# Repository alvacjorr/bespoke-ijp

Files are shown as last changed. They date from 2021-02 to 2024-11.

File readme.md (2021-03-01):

# bespoke-ijp



This repository is used for documents / code / notes related to the controller and software of the IEB bespoke inkjet printing rig. 
## Folder Structure
| Folder |  Description  | 
| ---| ---|
| `/application` | Code for the application/GUI |
| `/embedded` | Code for the uSteppers |
| `/docs` | Documentation |

## Workflow - Basics 
#### How do I get a copy of this repo?
- Install **Git**: https://help.github.com/en/github/getting-started-with-github/set-up-git
- Open up a terminal / command prompt and clone this repository: `git clone https://github.com/thekeeno/bespoke-ijp` which will give you a local copy of the main branch in the repository

#### Do I have to use a terminal?
- You can also use Git GUIs, e.g. https://desktop.github.com/ or https://www.gitkraken.com/

#### How do I keep my local copy updated?
- If you are on the main branch you can type `git pull`

#### How can I add / submit my changes?
- **The main main branch is protected, so you will have to create a separate branch and open a pull request.**
- The `main` branch should always reflect the newest agreed on version of the repository
- Make sure you branch off the latest state of main, i.e. on main type `git pull` or use `git fetch`
- To create a new branch use: `git checkout -b [branchname]`, e.g. `git checkout -b mg/new_branch`
- Make changes to files / add new files
- Take a look at the summary of changed files: `git status` 
- Add the new files to be tracked: `git add .` (to add all new files) or `git add code.m` (to add specific file)
- Commit the new changes (this creates a snapshot of repository state): `git commit -m "Change parameter gamma to 0.5"`
- Copy your new local branch with the new commits to the Github repository: `git push -u origin mg/new_branch`

- **Before your changes can be merged:** Make sure that you integrate the changes on `main` that others might have added in the meantime. This can be achieved by pulling the `main` changes to yout machine and then *merging* or preferably *rebasing* your commits onto the latest `main` version. See [here](https://gist.github.com/blackfalcon/8428401#keeping-current-with-the-master-branch) for a more detailed explanation.
- On https://github.com/oxfordcontrol/OxVentControl/ click on `Pull requests` -> `New Pull Request`. 
- Select `base:main` and `compare:mg/new_branch`
- All the changes can then be discussed in that pull request before they are approved and added to the main branch.
#### Useful git commands:
- https://rogerdudler.github.io/git-guide/
- https://confluence.atlassian.com/bitbucketserver/basic-git-commands-776639767.html
- http://ohshitgit.com/

## Workflow - Making Git collaboration easier 
A few steps everyone should take to make collaboration with Git easier:

#### Commit early and often
One commit should reflect one meaningful change to the code. Especially if we work on lots of different things at the same time, it is helpful if we create one meaningful commit for each significant change to the code. Notice that you don't have to commit all current changes at the same time. If you changed something in `A.cpp` and something different in `B.cpp`, you can do:
```bash
git add A.cpp
git commit -m "Fixed printing in A."
git add B.cpp
git commit -m "Changed parameters in B."
```
#### Combine temporary commits / clean up your history
If your recent 4 commits look like this `Fixed ABC`, `Work in progress`, `Working version` `Ups small fix` and you want to open a pull request to add this to the code you should first combine these commits into one commit. This can be done with an interactive  `git rebase`. To select the last 4 commits to squash, type:
```bash
git rebase -i HEAD~4
```
This should open an editor and show something like this:
```bash
pick d94e78 Fixed ABC     --- older commit
pick 4e9baa Work in progress
pick afb581 Working version  
pick 643d0e Ups small fix --- newer commit
```
Pick the oldest commit and squash the other ones into it by editing the file and saving it like this:
```bash
pick d94e78 Fixed ABC     --- older commit
s 4e9baa Work in progress
s afb581 Working version  
s 643d0e Ups small fix --- newer commit
```
You can then write a commit message for this combined commit. Combining commits can be very powerful, **but keep in mind that this rewrites the git history. Therefore never use the rebase on a remote branch where you know that other people rely on your history.**

[More info](https://www.internalpointers.com/post/squash-commits-into-one-git)

#### Write meaningful commit messages


Commit messages should make it easy to understand what particular change the commit implements. For more complex cases it can be helpful to write more than one sentence. To do that use the commit command without the message flag:
```bash
git commit
```
your default editor will open and you can write a longer form commit message. If you don't like the default editor you can set another one with:
```bash
git config --global core.editor "vim"
```

Follow the 7 rules of a great Git commit message

1. Separate subject from body with a blank line
2. Limit the subject line to 50 characters
3. Capitalize the subject line
4. Do not end the subject line with a period
5. Use the imperative mood in the subject line
6. Wrap the body at 72 characters
7. Use the body to explain what and why vs. how

[from here](https://chris.beams.io/posts/git-commit/)

#### Visualise the git tree before you merge
In order to not cause chaos with merges, it is helpful to take a look at the git commit tree and see where you currently are with your branch and where the branch you want to merge into currently is. You can either use a software package like [Gitkraken](https://www.gitkraken.com/) or alternatively use the command-line with:
```bash
git log --graph --decorate --oneline
```
If this is too long to remember you can create a Git Alias. On Unix systems type:
```bash
vim ~/.gitconfig
```
and add the line
```
[alias]
  gr = git log --graph --decorate --oneline
```
to the file.
#### Integrate the latest changes before opening a PR
If you are on the branch `my_fix` and want to open a PR to merge into `target_branch`, double-check if in the meantime any other changes happened on `target_branch` that might cause problems. To integrate the latest changes checkout the target branch:
```bash
git checkout target_branch
git pull origin target_branch
git checkout my_fix
```
To integrate the changes you can either `rebase` or `merge`. Rebasing is the cleaner way of the two as it doesn't introduce new merge commits. It essentially replays all of your new commits in `my_fix` onto the latest commit of `target_branch`. In some cases this will not go smoothly and you'll have to fix the conflicts as the commits are applied. **Again note that the rebase will rewrite history, so only do that if you know nobody else relies on the commits that will be rewritten**.

[Merging vs. Rebasing](https://www.atlassian.com/git/tutorials/merging-vs-rebasing)

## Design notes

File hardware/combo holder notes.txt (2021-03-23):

nozzle dia 3.5
depth 12.7

minicut width 1
height 4.577

photofluor small dia 5
large dia 9
depth 20

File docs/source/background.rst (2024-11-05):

Background and Motivation
==========

This section explains the main motivations for the development of the bespoke-ijp system, as well as a description of some of the work that precedes it.
Much of this section is copied verbatim from Alva Orr's transfer report.

Inkjet Printing
***************

Inkjet printing is a digital, non-contact manufacturing method which, broadly speaking, consists of launching droplets of fluid from a nozzle onto a substrate.
Inkjet printing is a large market, with an estimated size of \$34 billion in 2019(Mordor Intelligence). 
The most familiar usage of inkjet printing is in reprographics, which makes up around 90\% of the market, and includes commodity devices like desktop inkjet printers.

In the case of this system, Drop-On-Demand (DOD) is used.

Predecessor System
********************

The predecessor to this system, which ran using smaller stepper motors on belts, over a LabVIEW controller, currently still lives in the Fluids Lab.
It is thoroughly documented in Ellis Parry's DPhil thesis, soon to be available on ORA.
However, it has some limitations, especially with proprietary driver compatibility and dependence on closed-source software.
The new bespoke-ijp system was therefore conceived to remedy these issues. The major improvements are set to include:

- Use of closed-loop position control for maximum repeatability
- Dedicated stepper driver chips
- All built on open-source platforms (Arduino, Python)
- Cross-platform compatability (Windows, Linux in the works)
- Optional closed-loop heating control
- Support for synchronised motion and piezo pulses
- Basic scripting language, built on GCode, to allow for printing of patterns and similar routines

Comparable Systems
******************

This system can be thought of as a low-cost, flexible DIY alternative to the MicroFab JetLab system installed in the Holder building.
Although the commercial JetLab system is very accurate and reliable, it is not capable of integrating complex observation systems such as multiple high-speed cameras.

Relevent Publications and Literature
************************************

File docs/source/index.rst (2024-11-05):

IEB Bespoke Inkjet Printing
=======================================

This manual is for the Bespoke IEB Inkjet Printing (IJP) rig, a collaborative project between the `Fluid Dynamics Lab <http://www2.eng.ox.ac.uk/fluidlab>`_ and `Soft Matter Photonics <http://www2.eng.ox.ac.uk/smp>`_ groups in the Oxford University Department of Engineering Science.
Currently the person responsible for building and maintaining this rig is Alva Orr.

This documentation is still a Work In Progress. If there's any glaring omissions, please contact alva.orr@queens.ox.ac.uk.

.. toctree::
   :caption: Contents
   :maxdepth: 4

   background
   userguide
   building
   programmer
   autodoc/modules
   funcgen
   issues

Indices and tables
==================

* :ref:`genindex`
* :ref:`modindex`
* :ref:`search`

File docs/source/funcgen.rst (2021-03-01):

Function Generator Setup
========================

Aim 
******

We want to generate 10kHz square waves, that ramp up and down to various amplitudes ~175V.
The ramp up should be configurable to either be linear at varying rates, or in steps.

How

****

Unfortunately, the Tektronics AFG-2021 has some weird behavior with arbitrary waveforms and AM.
So we use the AFG-2021 as the modulator, and have a different (GWINSTEK?) AFG generate the 10kHz carrier.

Configuration of the AFG-2021
*****************************

1-Shot mode. around 100mHz. Lower voltage 0V. Higher voltage 5V.

Equation comes from PC. 

Configuration of the other function Generator
**********************************************

Set up so that at 0V Mod, the waveform is 0V p-p, and at 5V Mod, the output is XV p-p.

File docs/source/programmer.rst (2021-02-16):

Programmer's Documentation
==========================

The code for this project is split into two parts - Python code for the GUI and C++ embedded code for the uSteppers.
When navigating this code, it is strongly recommended to use Visual Studio Code with the C++, Python, Git and Arduino extensions.

In addition, this documentation is assembled using sphinx and ReadTheDocs.com.

Embedded 
*********

The core of the embedded firmware is loosely based on a GCode parser included with the uStepper's examples, but extended and upgraded to include more commands.

GUI Code
********

The classes, modules and functions that make this software work are all documented in the Python Module Guide.
This section is intended instead as a loose overview of the way the GUI operates.

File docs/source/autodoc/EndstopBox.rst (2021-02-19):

EndstopBox module
=================

.. automodule:: EndstopBox
   :members:
   :undoc-members:
   :show-inheritance:

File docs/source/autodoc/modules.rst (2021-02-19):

src
===

.. toctree::
   :maxdepth: 4

   EndstopBox
   SequenceHandler
   XYSerialInterface
   XY_commander
   constants
   conversions
   embedding_in_qt_sgskip
   plotter_example
   port_finder
   psu_serial
   testpsu

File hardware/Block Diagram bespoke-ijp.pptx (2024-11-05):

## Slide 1

PC

Photofluor II Light Source

Polariser

RS232

JetDrive III

Nozzle Heatblock

GPD-43035
Power Supply

USB Camera

Γ

2

1

Polarised Optical Microscopy Path

Slide Holder

Shadowgraphy Path

H

T

LED

Γ

H

T

PhlatLight LED Driver

MAX31855

Analyzer + Camera

Γ

uStepper X

Motor X

Nozzle

DIGITAL OUT

Camera

LED

SPI

uStepper Y

Motor Y

Piezo Waveform

USB/Serial

TTL Trigger (5V)

Thermocouple Wire

Heater Cable (24V)

Heater Module

Thermocouple (K-Type)

Trigger Input

H

T

Γ

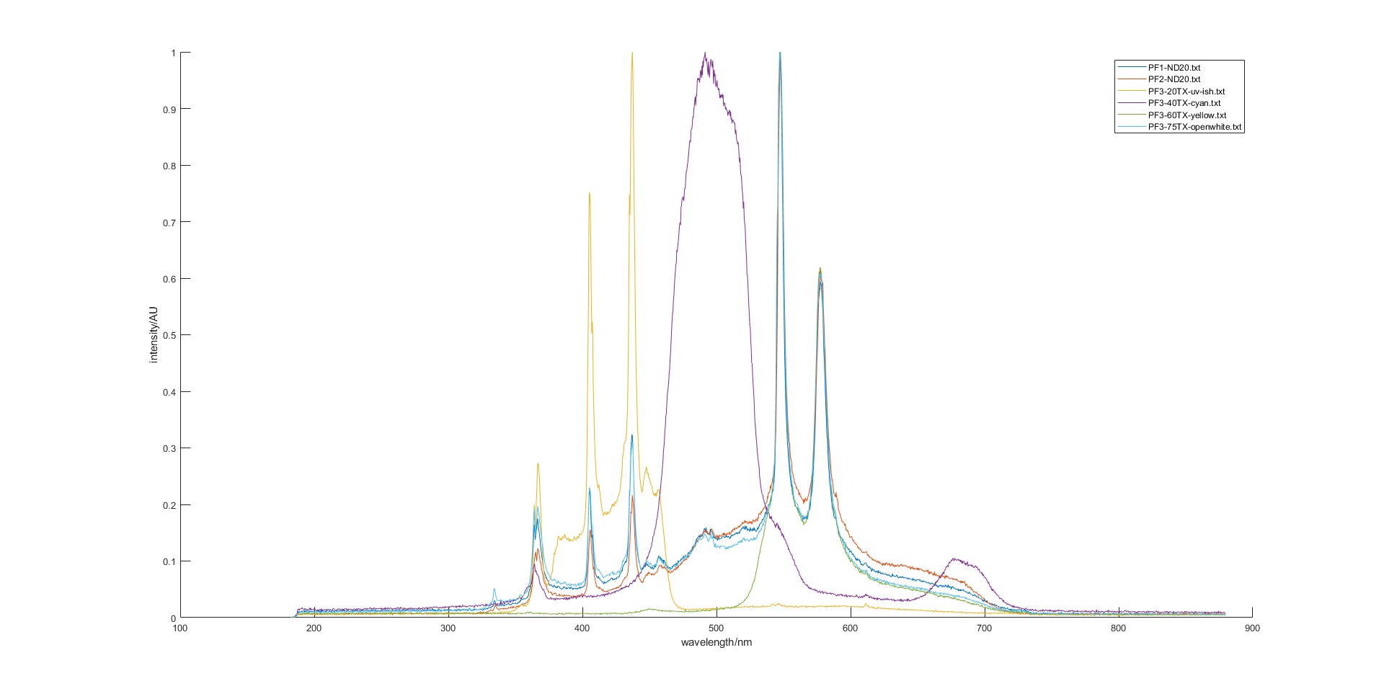
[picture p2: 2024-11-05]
photofluor_spectra/spectra.jpg

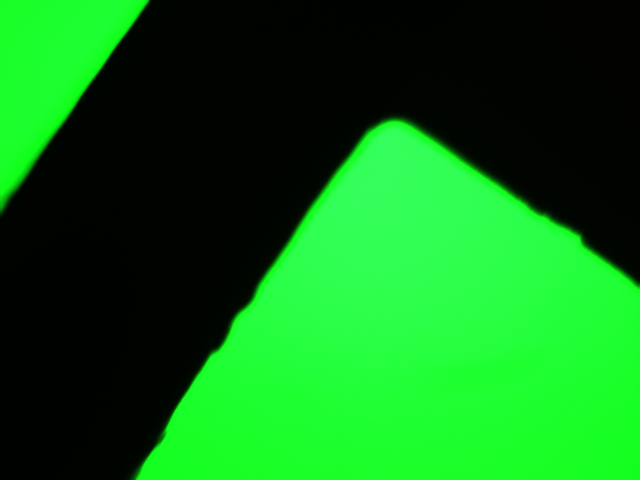
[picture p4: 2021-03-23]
img/chopper-good.bmp

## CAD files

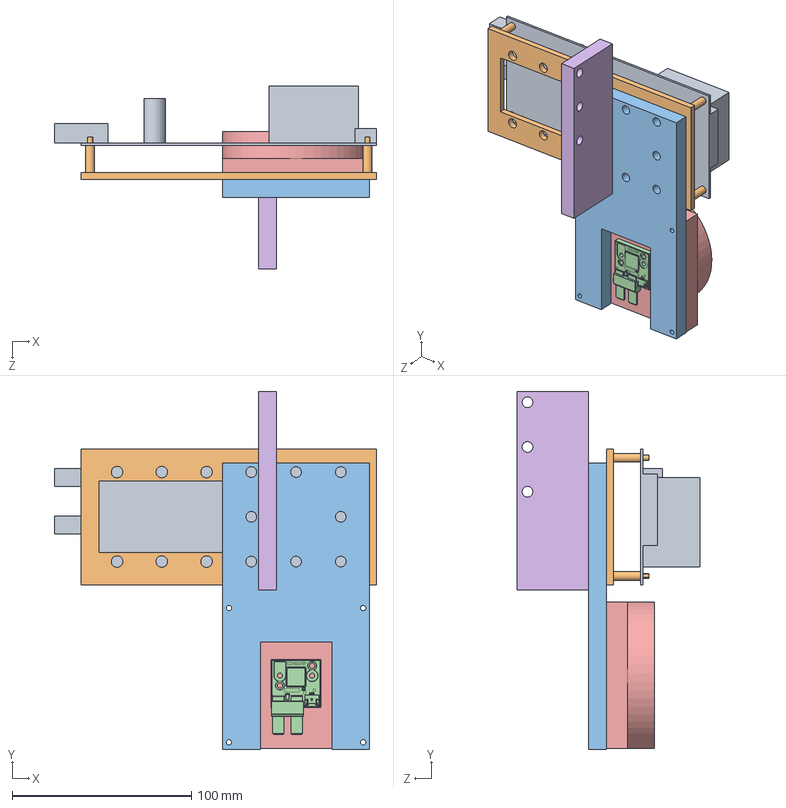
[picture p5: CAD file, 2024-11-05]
hardware/assemblies/LED-holder-assy-righthand.SLDASM
180.0 x 200.0 x 102.5 mm
Phlatlight-template
phlatlight-pcb-holder
phlatlight-led-holder
DWG-002051_PT-120-G_DF_111618.step
phlatlight-heatsink
phlatlight-support-A

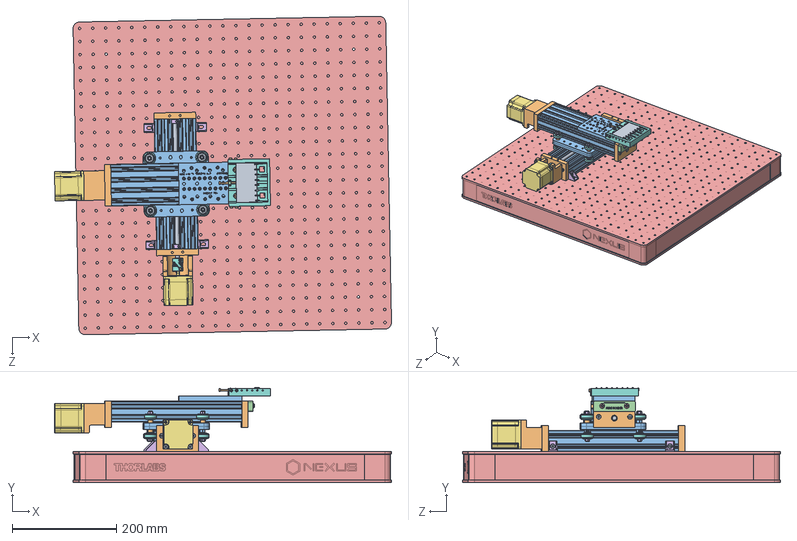
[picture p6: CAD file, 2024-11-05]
hardware/c-beam/xy-stage.SLDASM
646.5 x 183.0 x 610.8 mm
Low Profile Screw M5 x 36
C-Beam End Mount x 4
C-Beam 40x80x250 Linear Rail x 2
Ball Bearing 8 x 16 x 5 x 4
Shim Washer 8mm x 4
Lock Collar 8mm x 4
Nema 23 Stepper Motor x 2
Flexible Coupling 0.25in x 8mm x 2
8mm leadscrew 290mm x 2
motor-offset x 2
C-Beam Gantry Plate XLarge x 2
8mm Acme Anti Backlash Nut Block x 2
Aluminum Spacer 3mm x 4
Nylon Insert Lock Nut M5 x 12
Precision Shim 10 x 5 x 1 x 20
Xtreme Solid V Wheel x 8
Ball Bearing 5 x 16 x 5 x 16
Aluminum Spacer 6mm x 4
Eccentric Spacer 6mm x 4
crude-slide-holder
socket button head screw_bsi x 2
Cast Corner Bracket x 4
Tee Nut x 4
complex-slide-holder-A
complex-slide-holder-B
socket head cap screw_bsi x 9
c-beam-to-6mm-optical-adapter-plate
complex-slide-holder-C
B6060A-Solidworks

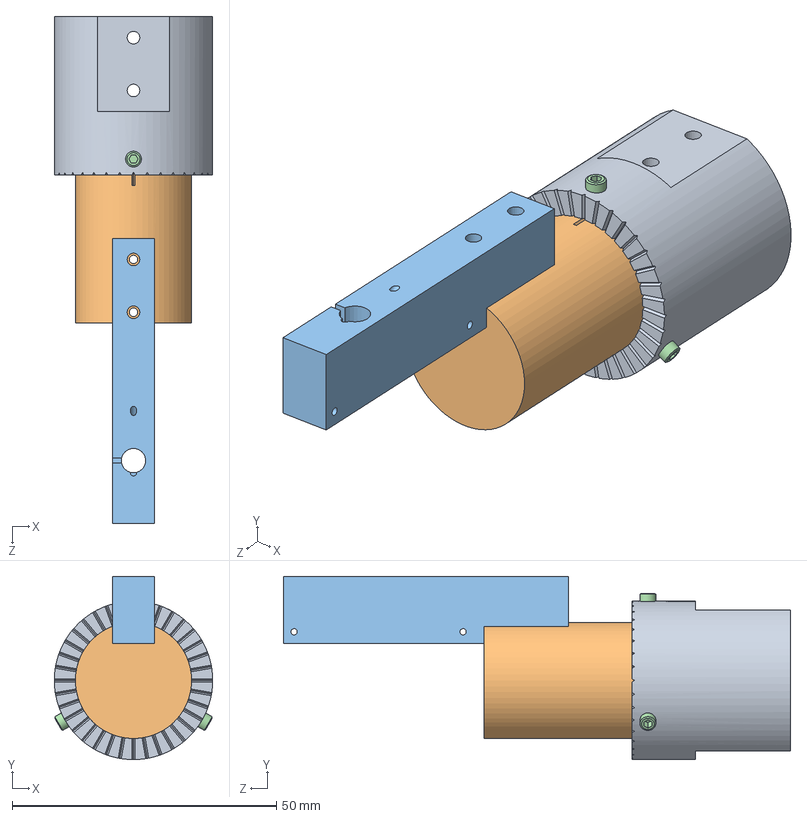
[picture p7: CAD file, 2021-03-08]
hardware/microfab/microfab rotor sheath/assembly.SLDASM
30.0 x 34.7 x 96.0 mm
microfab rotor A
microfab rotor B
microfab heating sheath Large
socket set screw cone point_bsi x 3

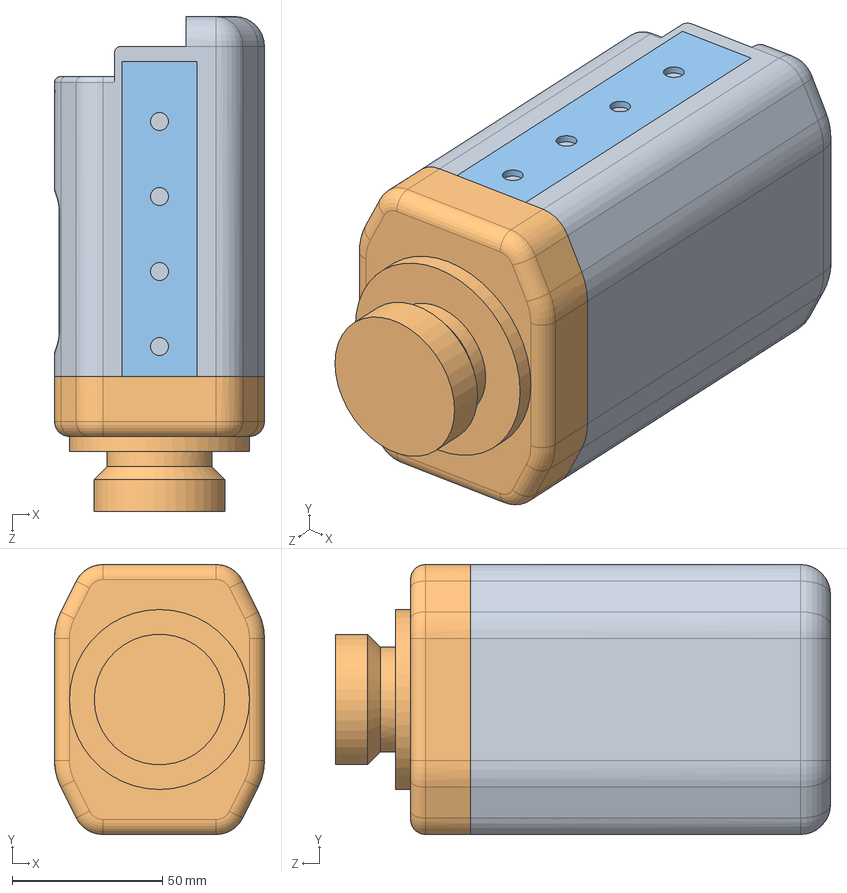
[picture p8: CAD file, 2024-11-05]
hardware/Miro By Ben/miro.SLDASM
70.0 x 90.0 x 165.0 mm
mirobottom
mirotop
mirostrip

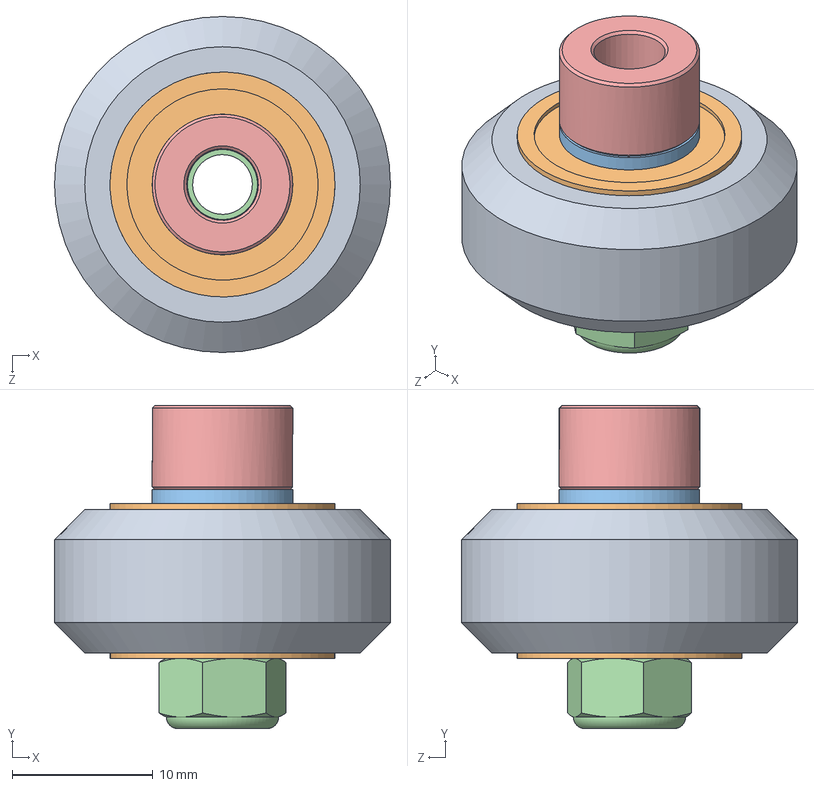
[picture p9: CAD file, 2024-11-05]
hardware/SW2014 Parts Library 1.6/Assemblies/Wheels/Xtreme V Wheel.SLDASM
23.9 x 23.0 x 23.9 mm
Xtreme Solid V Wheel
Ball Bearing 5 x 16 x 5 x 2
Precision Shim 10 x 5 x 1 x 2
Nylon Insert Lock Nut M5
Aluminum Spacer 6mm

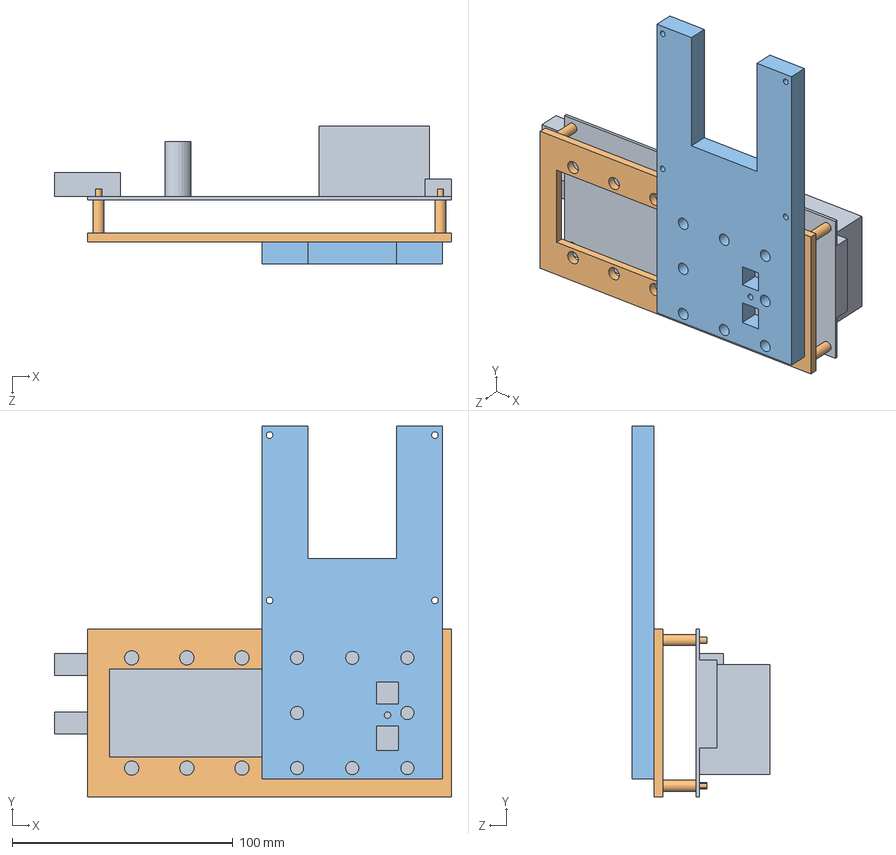
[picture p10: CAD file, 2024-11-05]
hardware/assemblies/LED-holder-assy-lefthand.SLDASM
180.0 x 168.0 x 62.5 mm
Phlatlight-template
phlatlight-pcb-holder
phlatlight-led-holder

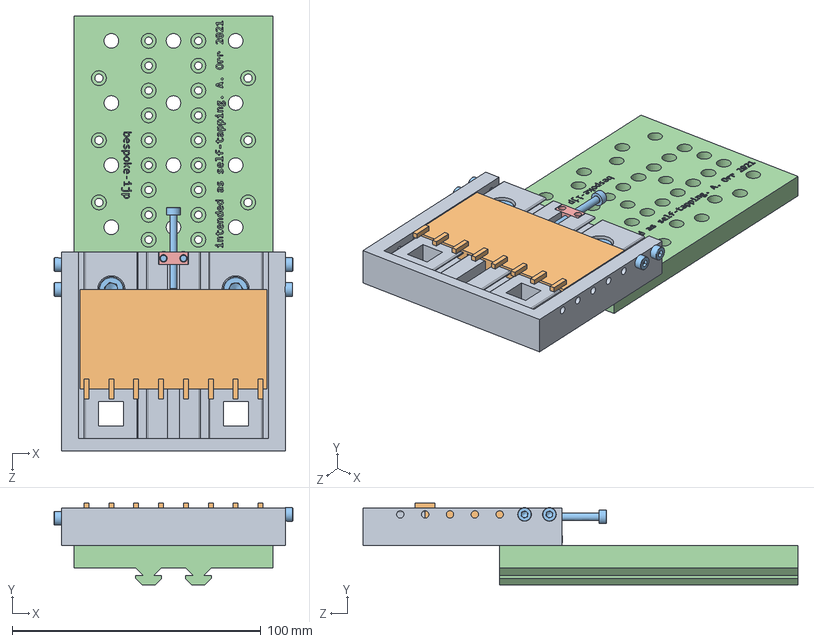
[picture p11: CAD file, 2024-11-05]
hardware/c-beam/complex-slide-holder-assy.SLDASM
96.0 x 32.8 x 175.0 mm
complex-slide-holder-A
complex-slide-holder-B
socket head cap screw_bsi x 9
c-beam-to-6mm-optical-adapter-plate
complex-slide-holder-C

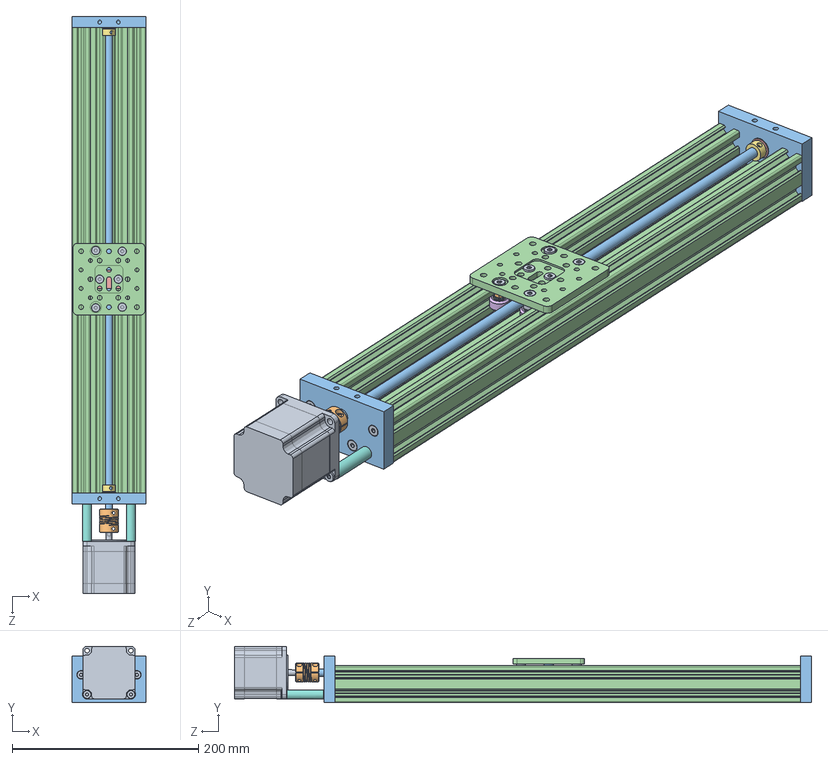
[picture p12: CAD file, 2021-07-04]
hardware/SW2014 Parts Library 1.6/Assemblies/C-Beam Linear Actuator/C-Beam Linear Actuator 500mm.SLDASM
80.0 x 60.7 x 620.0 mm
Low Profile Screw M5 x 16
Nylon Insert Lock Nut M5 x 6
C-Beam End Mount x 2
C-Beam 40x80x500 Linear Rail
Ball Bearing 8 x 16 x 5 x 2
Shim Washer 8mm x 2
Lock Collar 8mm x 2
Aluminum Spacer 40mm x 2
Nema 23 Stepper Motor
Flexible Coupling 0.25in x 8mm
8mm leadscrew 540mm
C-Beam Gantry Plate
8mm Acme Nut Block
Xtreme Mini V Wheel x 4
Ball Bearing 5 x 10 x 4.2 x 8
Precision Shim 8 x 5 x 1 x 8
Aluminum Spacer 6mm x 2
Mini Eccentric Spacer 6mm x 2
Aluminum Spacer 3mm x 2

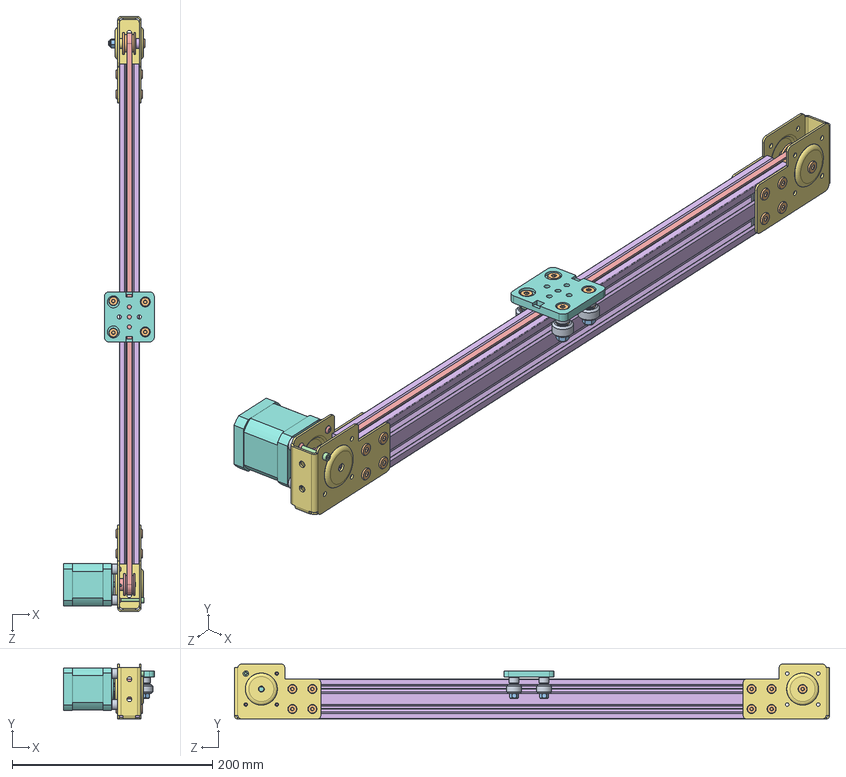
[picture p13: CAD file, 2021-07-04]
hardware/SW2014 Parts Library 1.6/Assemblies/Mini V Linear Actuator/Mini V Linear Actuator 500mm.SLDASM
90.6 x 54.9 x 594.7 mm
Double Tee Nut x 8
Low Profile Screw M5 x 21
Nylon Insert Lock Nut M5 x 5
Button Head Socket Cap Screw M3 x 4
V-Slot 20x40x500 Linear Rail
Linear Actuator End Mount x 2
Nema 17 Stepper Motor
Aluminum Spacer 6mm x 6
Smooth Idler Pulley Wheel
Ball Bearing 5 x 16 x 5 x 2
Nylon Spacer 0.125in
GT2 Timing Pulley 30 Tooth
Aluminum Spacer .25in
Aluminum Spacer .125in
Mini V Wheel Plate
Delrin Mini V Wheel x 4
Ball Bearing 5 x 10 x 4.2 x 8
Precision Shim 8 x 5 x 1 x 8
Mini Eccentric Spacer 6mm x 2
GT2 Belt 1140mm

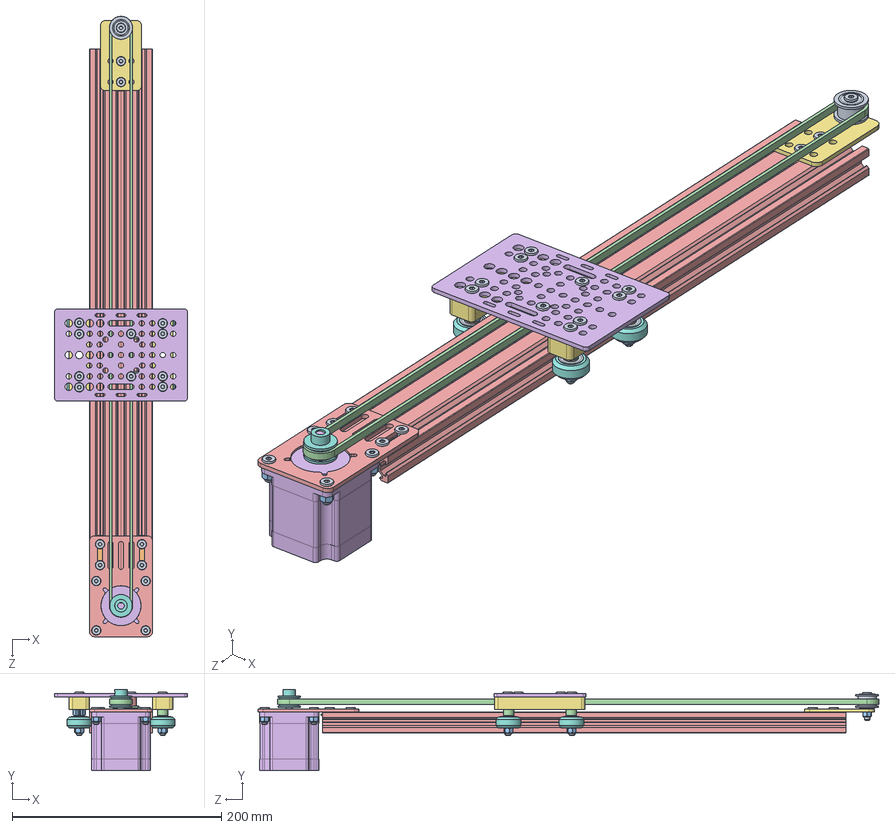
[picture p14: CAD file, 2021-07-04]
hardware/SW2014 Parts Library 1.6/Assemblies/V Slot Belt Driven Actuator/Nema 23 V Slot Belt Driven Actuator 500mm.SLDASM
127.0 x 77.6 x 592.7 mm
Low Profile Screw M5 x 21
Double Tee Nut x 3
Nylon Insert Lock Nut M5 x 9
Tee Nut x 2
V-Slot 20x60x500 Linear Rail
V-Slot Gantry Plate 20-80mm
Spacer Block x 2
Solid V Wheel x 4
Ball Bearing 5 x 16 x 5 x 10
Precision Shim 10 x 5 x 1 x 8
Eccentric Spacer 6mm x 2
Aluminum Spacer 6mm x 2
Motor Mount Plate Nema 23
Nema 23 Stepper Motor
Idler Pulley Plate
GT3 Timing Pulley 20 Tooth
Smooth Idler Pulley Wheel
Nylon Spacer 0.125in
Precision Shim 8 x 5 x 1
GT3 Belt 1160mm
Aluminum Spacer 9mm x 2

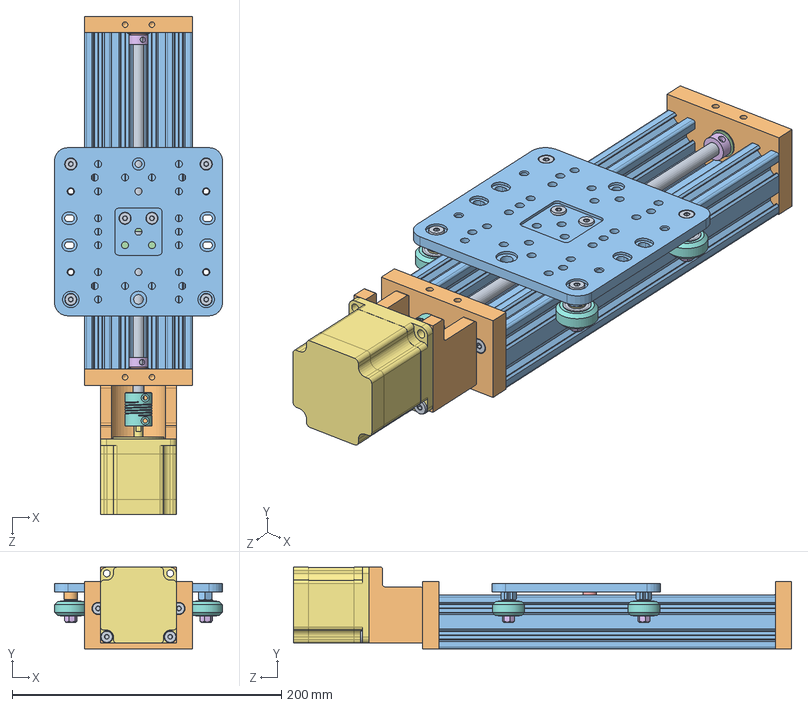
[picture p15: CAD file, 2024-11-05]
hardware/c-beam/modded-linear-actuator.SLDASM
125.0 x 60.7 x 370.0 mm
Low Profile Screw M5 x 16
C-Beam End Mount x 2
C-Beam 40x80x250 Linear Rail
Ball Bearing 8 x 16 x 5 x 2
Shim Washer 8mm x 2
Lock Collar 8mm x 2
Nema 23 Stepper Motor
Flexible Coupling 0.25in x 8mm
8mm leadscrew 290mm
motor-offset
C-Beam Gantry Plate XLarge
8mm Acme Anti Backlash Nut Block
Aluminum Spacer 3mm x 2
Nylon Insert Lock Nut M5 x 6
Precision Shim 10 x 5 x 1 x 10
Xtreme Solid V Wheel x 4
Ball Bearing 5 x 16 x 5 x 8
Aluminum Spacer 6mm x 2
Eccentric Spacer 6mm x 2

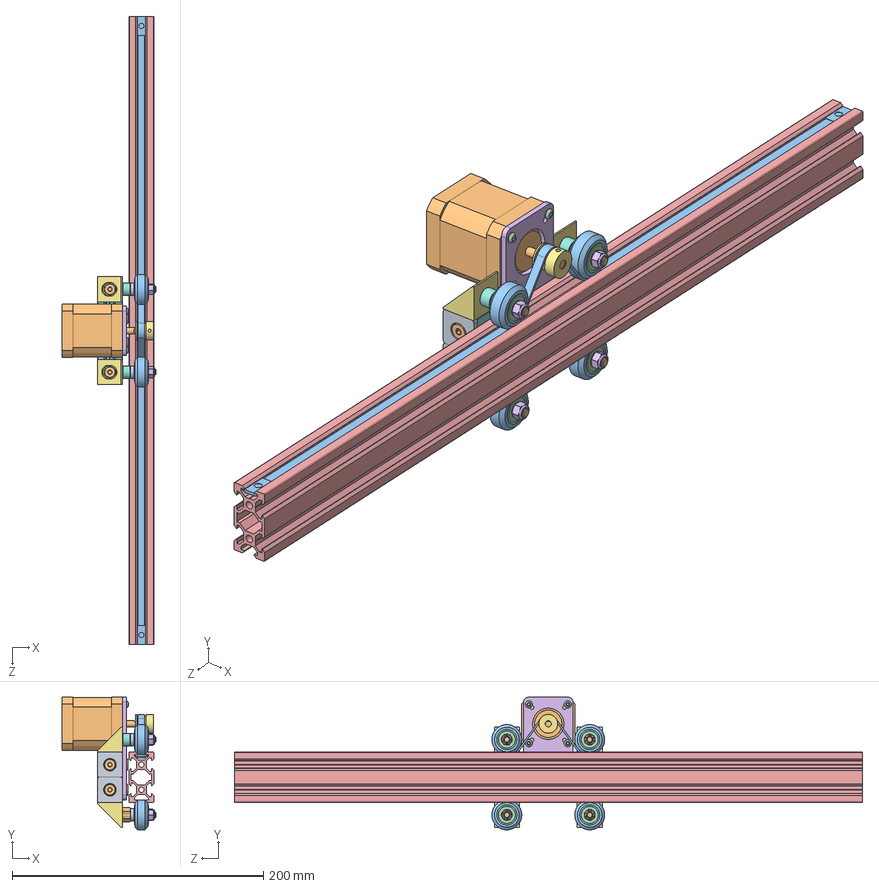
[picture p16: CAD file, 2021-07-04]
hardware/SW2014 Parts Library 1.6/Assemblies/V Slot Belt and Pinion Actuator/Mini V Slot Belt and Pinion Actuator 500mm.SLDASM
74.5 x 105.7 x 500.0 mm
Double Tee Nut x 2
Low Profile Screw M5 x 16
Tee Nut x 6
Button Head Socket Cap Screw M3 x 4
V-Slot 20x40x500 Linear Rail
Motor Mount Plate Nema 17
Black Angle Corner Connector x 4
V-Slot 20x40x80 Linear Rail
End Cap x 4
Nema 17 Stepper Motor
Solid V Wheel x 4
Ball Bearing 5 x 16 x 5 x 8
Precision Shim 10 x 5 x 1 x 4
Nylon Insert Lock Nut M5 x 4
GT2 Timing Pulley 20 Tooth
Aluminum Spacer .25in x 2
Aluminum Spacer .125in x 4
Eccentric Spacer 0.25in x 2
GT2 Belt 530mm

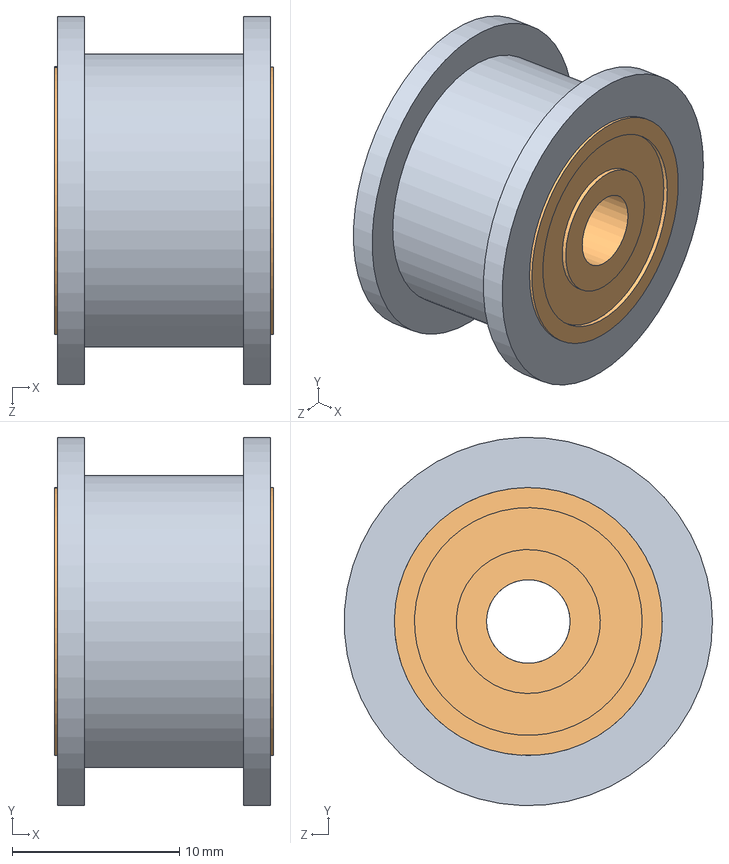
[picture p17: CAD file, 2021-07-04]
hardware/SW2014 Parts Library 1.6/Assemblies/Wheels/Smooth Idler.SLDASM
13.1 x 22.0 x 22.0 mm
Smooth Idler Pulley Wheel
Ball Bearing 5 x 16 x 5 x 2
Nylon Spacer 0.125in

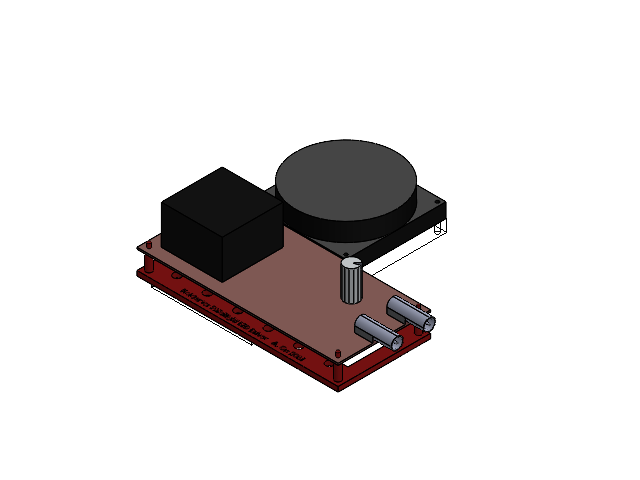
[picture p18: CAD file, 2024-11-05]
hardware/Luminus/Subassy-phatlight-full-system.SLDASM
phlatlight-led-holder
phlatlight-pcb-holder
phlatlight-DK-driver-board
PT-120-LED
phlatlight-heatsink

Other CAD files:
hardware/SW2014 Parts Library 1.6/Assemblies/Wheels/Solid V Wheel.SLDASM
hardware/assemblies/Subassy-Lens-Post.SLDASM
hardware/krontech-microscope-lens/krontech-microscope-lens-full.SLDASM
hardware/assemblies/Subassy-Mirror-Pillar.SLDASM
hardware/ITO Etching Templates/ITOsegment1.SLDPRT
hardware/ITO Etching Templates/etching-template.SLDPRT
hardware/ITO Etching Templates/glass-slide-15-30.SLDPRT
hardware/ITO Etching Templates/ito-clipper.SLDPRT
hardware/ITO Etching Templates/slide-storage.SLDPRT
hardware/ITO Etching Templates/solder-wire.SLDPRT
hardware/Luminus/phlatlight-DK-driver-board.SLDPRT
hardware/Luminus/phlatlight-heatsink.SLDPRT
hardware/Luminus/phlatlight-led-holder.SLDPRT
hardware/Luminus/phlatlight-pcb-base.SLDPRT
hardware/Luminus/phlatlight-pcb-holder.SLDPRT
hardware/Luminus/phlatlight-standoff.SLDPRT
hardware/Luminus/phlatlight-support-A.SLDPRT
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

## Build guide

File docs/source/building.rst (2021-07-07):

Assembling a new bespoke-ijp system
===================================

The following instructions are advice only, and are followed at the reader's risk.
The writer(s) accept no responsibility for any inaccuracies.

Parts List
**********

This system is almost entirely made of off-the-shelf or 3D-printed parts.

Note: this is not exhaustive!

- An optical table
- A comedically large quantity of 
- 2x `OpenBuilds C-Beam Linear Actuator <https://ooznest.co.uk/product/c-beam-linear-actuator>`_

  - Actuator Length 250mm
  - NEMA23 Stepper Motor
  - XL Gantry Plate
  - No C-Beam Motor Standoff
  - uStepper S Controller Board

- A power supply (3A, 24V) for the motors
- Probably a 3D printer! To make extra bits with...
- A Windows computer to install the software on (Linux compatability is in the works)
- A programmable power supply for the heater beds
- An inkjet nozzle system (MicroFab or equivalent)
- An optical observation system (highspeed camera, polarised filters, microscope lens or similar)

Assembling the rails
*******************

OpenBuilds have instructions on their `website <https://openbuilds.com/builds/c-beam%E2%84%A2-linear-actuator.1955/>`_ to help you assemble the rails. Pictures also on their way!

Software Prerequisites
**********************

Installing the software
***********************

Prerequisites
-------------

You will need the following software installed:

- Python 3.7 with pip
- Arduino IDE 
- Git (and Git Bash if on windows)
- Arduino libraries and board profiles from the `uStepperS readme <https://github.com/uStepper/uStepperS>`_

Downloading the project
-----------------------

Open bash (linux/macOS) or Git Bash (Windows). Navigate to the folder you want to install the software in and enter the following:
::

    git clone https://github.com/thekeeno/bespoke-ijp

This will download the main repository to your system and put it in a folder called bespoke-ijp. 

Installing Python libraries
-----------------------------

Next, move into the project's root folder::

    cd bespoke-ijp

If you have a python venv, now is the time to activate it. If not, don't worry about it. To download the python libraries needed for this project, run::

    pip install -r requirements.txt

This may take a while. 

Optional: Add Function Generators
---------------------------------

If you are using this software with a Tektronix AFG2021 under Windows, you will need to install TekVISA.
Under Linux, this may not be necessary, but may require a tweak to the pyvisa setup.
At some point I may implement automatic switching.

A GW INSTEK AFG-2105 does not require a driver, instead being directly addressable as a serial port (like the Arduinos are!)

Uploading the firmware to the uSteppers
----------------------------------------

This can be done via Arduino IDE, arduino-cli and Visual Studio Code. In this section we will use the Arduino IDE.
The core firmware is located in embedded/src/XY_commander/XY_commander.ino.
Open this in Arduino IDE.
To verify you have the correct library configuration, click the tick button on the top bar.
This will compile the firmware but not upload it.
If this fails, check that you have selected uStepepr S as the board, and have downloaded the requisite Arduino libraries.

Once you know you can compile the firmware, it's time to upload it.
Ensure the uSteppers are powered externally and connected by USB.
Select the COM or tty port associated with your uStepper and click Upload.
Repeat for the second board.

Registering the X and Y axes with the GUI
------------------------------

To distinguish between the X and Y rails, simply specifying a COM or tty port can result in guesswork.
To simplify this process, the first time the program is run, it will look for a configuration file (ports_serial.py) with some serial numbers in it.
If this file does not exist, it will promt the user and make a new one.

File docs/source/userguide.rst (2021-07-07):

User's Guide
============

Hardware Overview
*****************

The system consists of:

- Motor Power Supply
- Heater Power Supply (GW INSTEK GPD-X303S)
- Control PC
- XY Translation Stage
- Heating elements (nozzle and bed)
- Microfab nozzles
- MicroFab JetDrive III
- Imaging setup (not documented here)

Connections
***********

Before beginning any experiment, ensure that the following connections are made:

- USB cables from both uSteppers to the PC
- Power from the motor PSU (24V) to the two motor controllers
- Power from the LED PSU (12V) to the Phlatlight LED driver
- USB cable from the GPD-4303S heater power supply to the PC
- Nozzle and bed heating elements to the heater PSU with banana plugs
- Thermocouples inside the nozzle and bed heatblocks
- RS-232 cable from the JetDrive III
- USB 3.0 cable from the camera to the PC

.. warning::
  It is crucial that the thermocouples are properly attached to the heating blocks. Without temperature sensors the system cannot regulate its own temperature and may engage in a thermal runaway.

Turning on the system
********************

In order:

#. Power on the controlling computer and log in
#. Power on the heater power supply (GW INSTEK GPD-X303S)

  * The power supply should say USB YES on its front panel.
  * Do not touch any controls on the front panel of the power supply.

#. Power on the motor power supply at the wall
#. Power on the LED power supply at the wall
#. Start the main software by running XY_commander.py 

  * This can be achieved either via VS Code or from the PRINTING.bat file on the desktop.

#. Open IC Capture 2.4 (link on desktop)
#. Open JetServer 4 (link on desktop)

Configuring IC Capture 2.4
**************************

.. warning::
  It is very important that you use IC Capture 2.4 - version 2.5 seems to be unable to enable the trigger on the camera.

#. If it does not automatically open, open the correct usb camera (DFK 23U618).
#. Right click the image and click 'Properties', and ensure the following settings are correctly set:

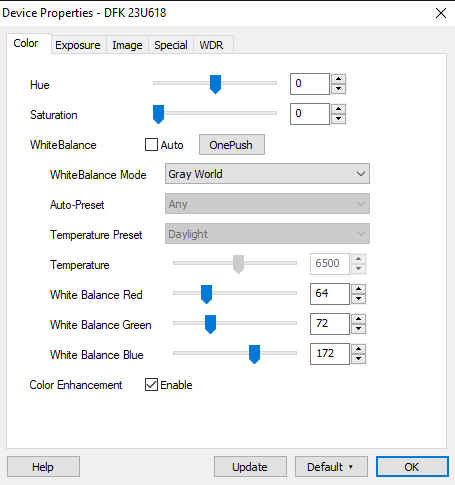
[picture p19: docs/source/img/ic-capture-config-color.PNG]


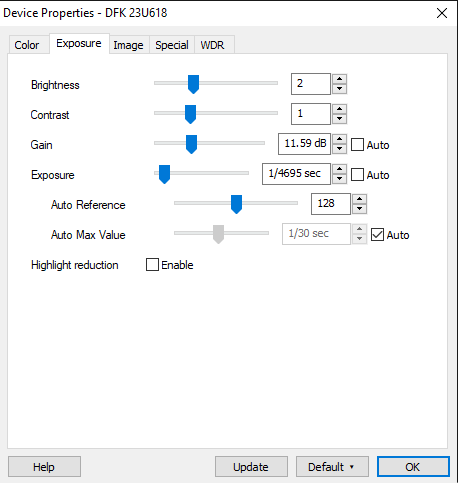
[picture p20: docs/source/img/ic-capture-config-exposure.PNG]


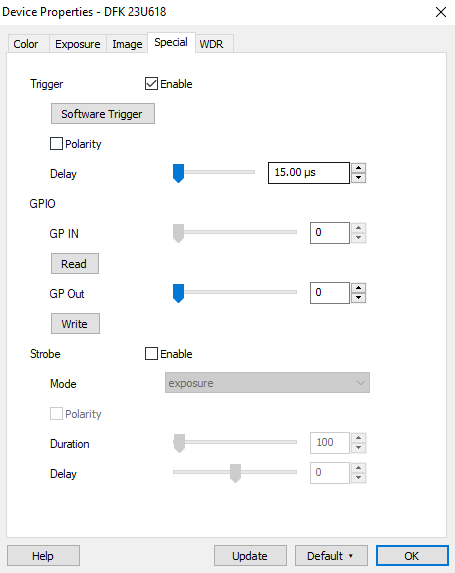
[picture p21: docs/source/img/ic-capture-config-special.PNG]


Configuring JetServer
*********************

JetServer tends to take care of itself - if you know how to use it then for the most part you should be fine.
The most important thing is to set the trigger mode to 'External' so that bespoke-ijp can control it.

Using the GUI
*************

GUI is in progress - this section is very subject to change!

Trigger Configuration
---------------------

Heater Control
--------------

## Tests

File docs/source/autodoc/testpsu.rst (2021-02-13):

testpsu module
==============

.. automodule:: testpsu
   :members:
   :undoc-members:
   :show-inheritance:

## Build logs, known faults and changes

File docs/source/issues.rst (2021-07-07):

Known Issues
============

See also https://github.com/thekeeno/bespoke-ijp/issues

Rate of PSU Polling
*******************

The GW INSTEK power suplpy sued may take upwards of 50ms to reply to requests for data.
This sets a hard limit on the rate at which currents and voltages may be retrieved for the PID control.
It can also slow down the program's UI from time to time.

Initialisation of uSteppers
***************************

Sometimes the uSteppers will not initialise their serial comms correctly when powered on.
Usually this corresponds to an error message in the GUI saying 'parsing failed' or similar.
To get around this, try power cycling the uSteppers (unlplug from USB and switch off the 24V rail).

Backlash
********

The system definitely has some backlash. The exact amount is yet to be quantified however!

Thermocouple Grounding
**********************

The MAX31855 boards are not compatible with grounded thermocouples.
If you ground the thermocouple (for example by putting it in contact with the optical table) it will return values of NAN.
This will prevent the PID loop from running, causing a loss of temperature control.
There is currently no auto-detect system for this error so do keep an eye out for it.
Watch out for messages like "TEMP N NAN B0.00"

Camera Software
***************

The more recend IC Capture 2.5 software occasionally has problems enabling the external trigger on the DFK USB camera.
To get around this, use the older version 2.4!

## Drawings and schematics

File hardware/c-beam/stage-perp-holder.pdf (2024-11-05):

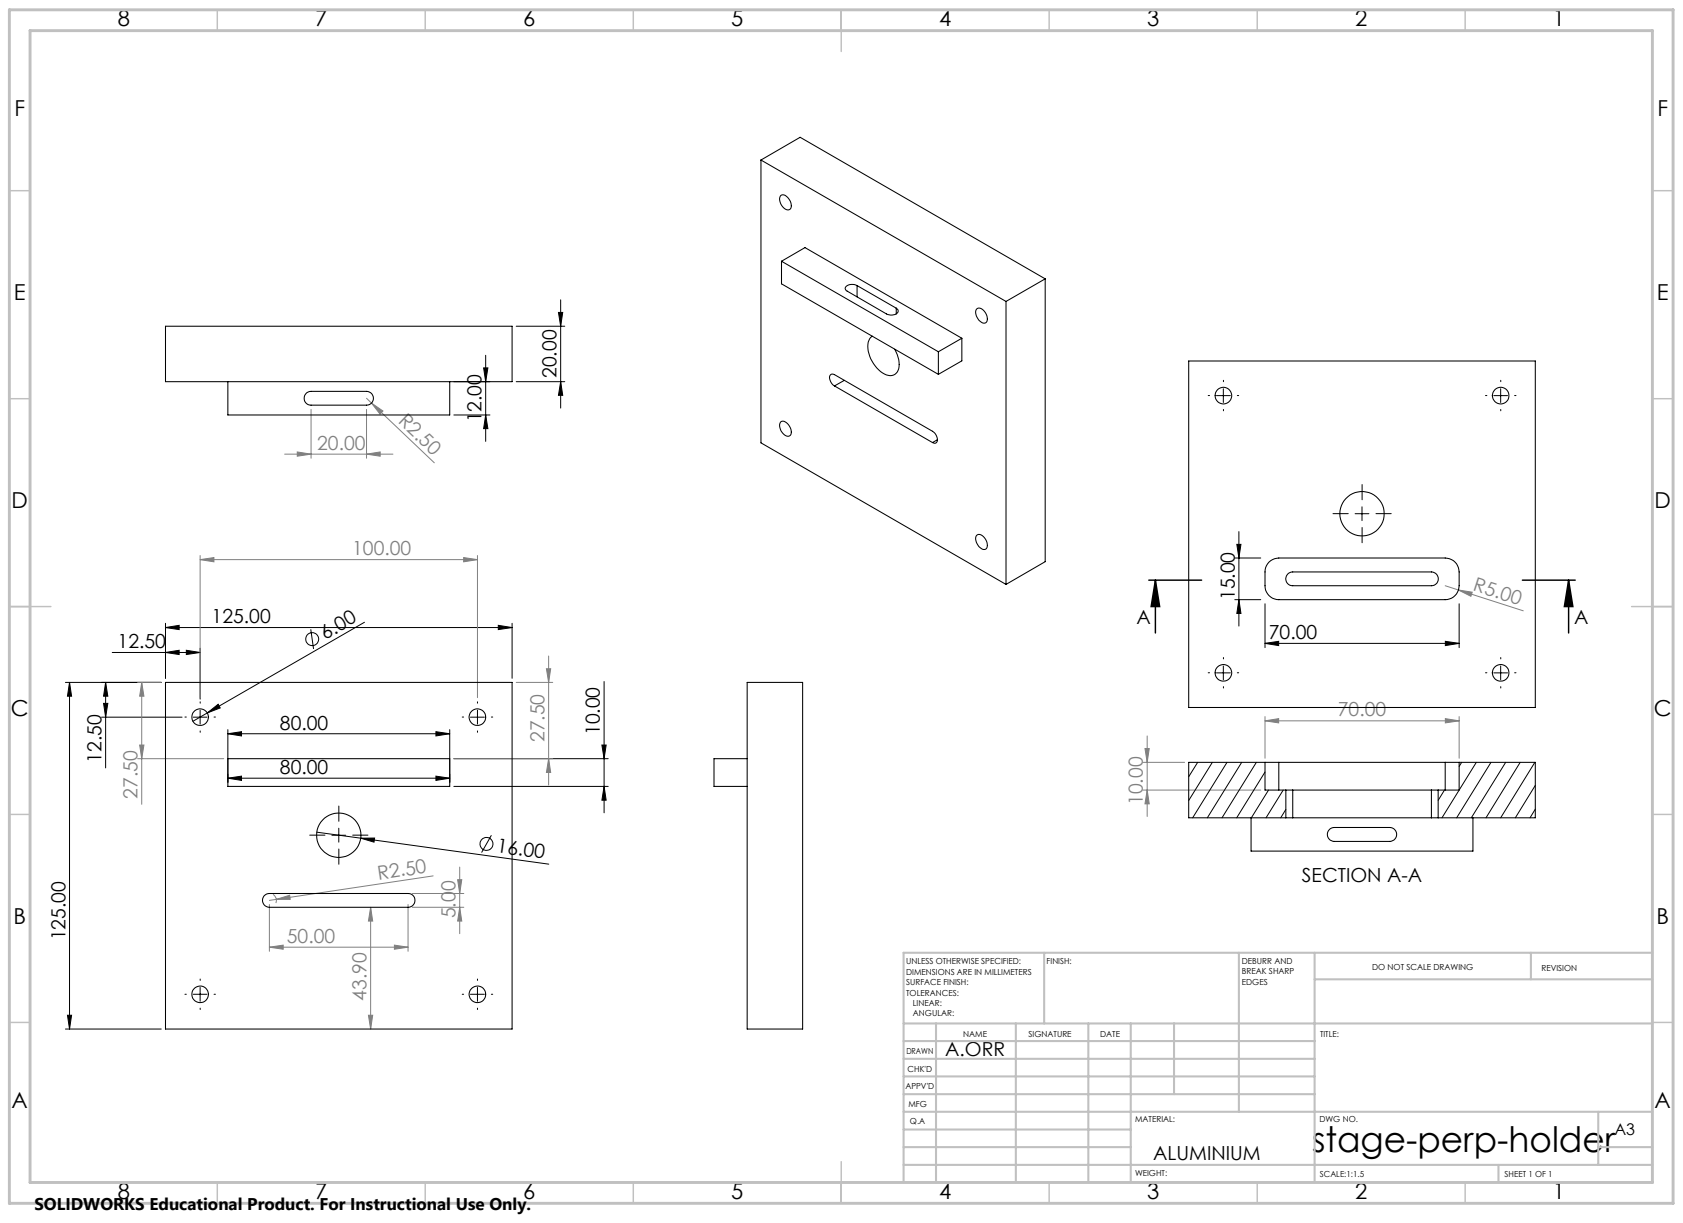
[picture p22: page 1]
SECTION A-A; FINISH:; DEBURR AND; BREAK SHARP; DO NOT SCALE DRAWING; REVISION; SCALE:1:1.5; SHEET 1 OF 1

UNLESS OTHERWISE SPECIFIED:
DIMENSIONS ARE IN MILLIMETERS
SURFACE FINISH:
TOLERANCES:
LINEAR:
ANGULAR:

DRAWN | A.ORR

NAME | SIGNATURE | DATE | | | | TITLE:

CHK'D
APPV'D
MFG
Q.A | | | | MATERIAL: ALUMINIUM | DWG NO. stage-perp-holder | A3

SOLIDWORKS Educational Product. For Instructional Use Only.

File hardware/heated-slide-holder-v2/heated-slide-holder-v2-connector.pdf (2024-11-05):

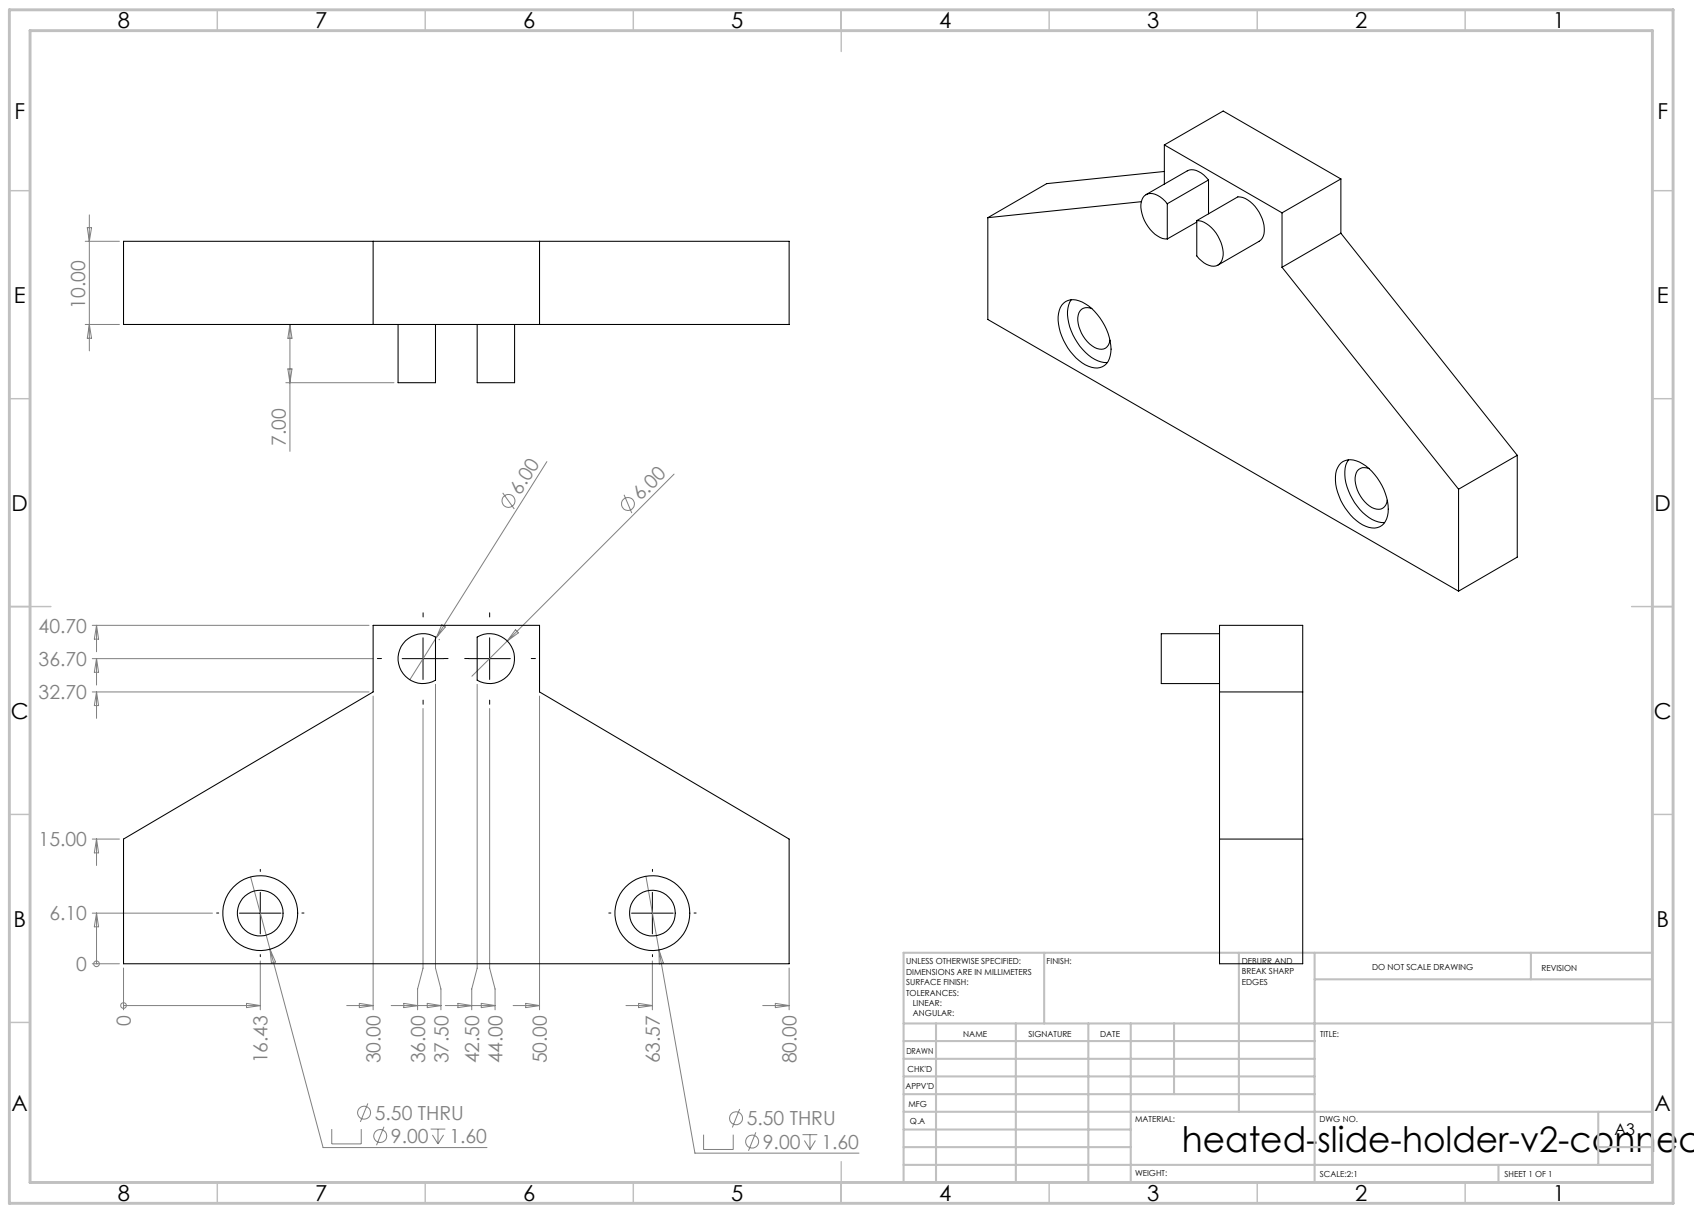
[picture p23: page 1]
5.50 THRU 9.00 1.60; FINISH:; DEBURR AND; BREAK SHARP; DO NOT SCALE DRAWING; REVISION; SCALE:2:1; SHEET 1 OF 1

UNLESS OTHERWISE SPECIFIED:
DIMENSIONS ARE IN MILLIMETERS
SURFACE FINISH:
TOLERANCES:
LINEAR:
ANGULAR:

NAME | SIGNATURE | DATE | | | | TITLE:

DRAWN
CHK'D
APPV'D
MFG
Q.A | | | | MATERIAL: | DWG NO. | A3

heated-slide-holder-v2-connector

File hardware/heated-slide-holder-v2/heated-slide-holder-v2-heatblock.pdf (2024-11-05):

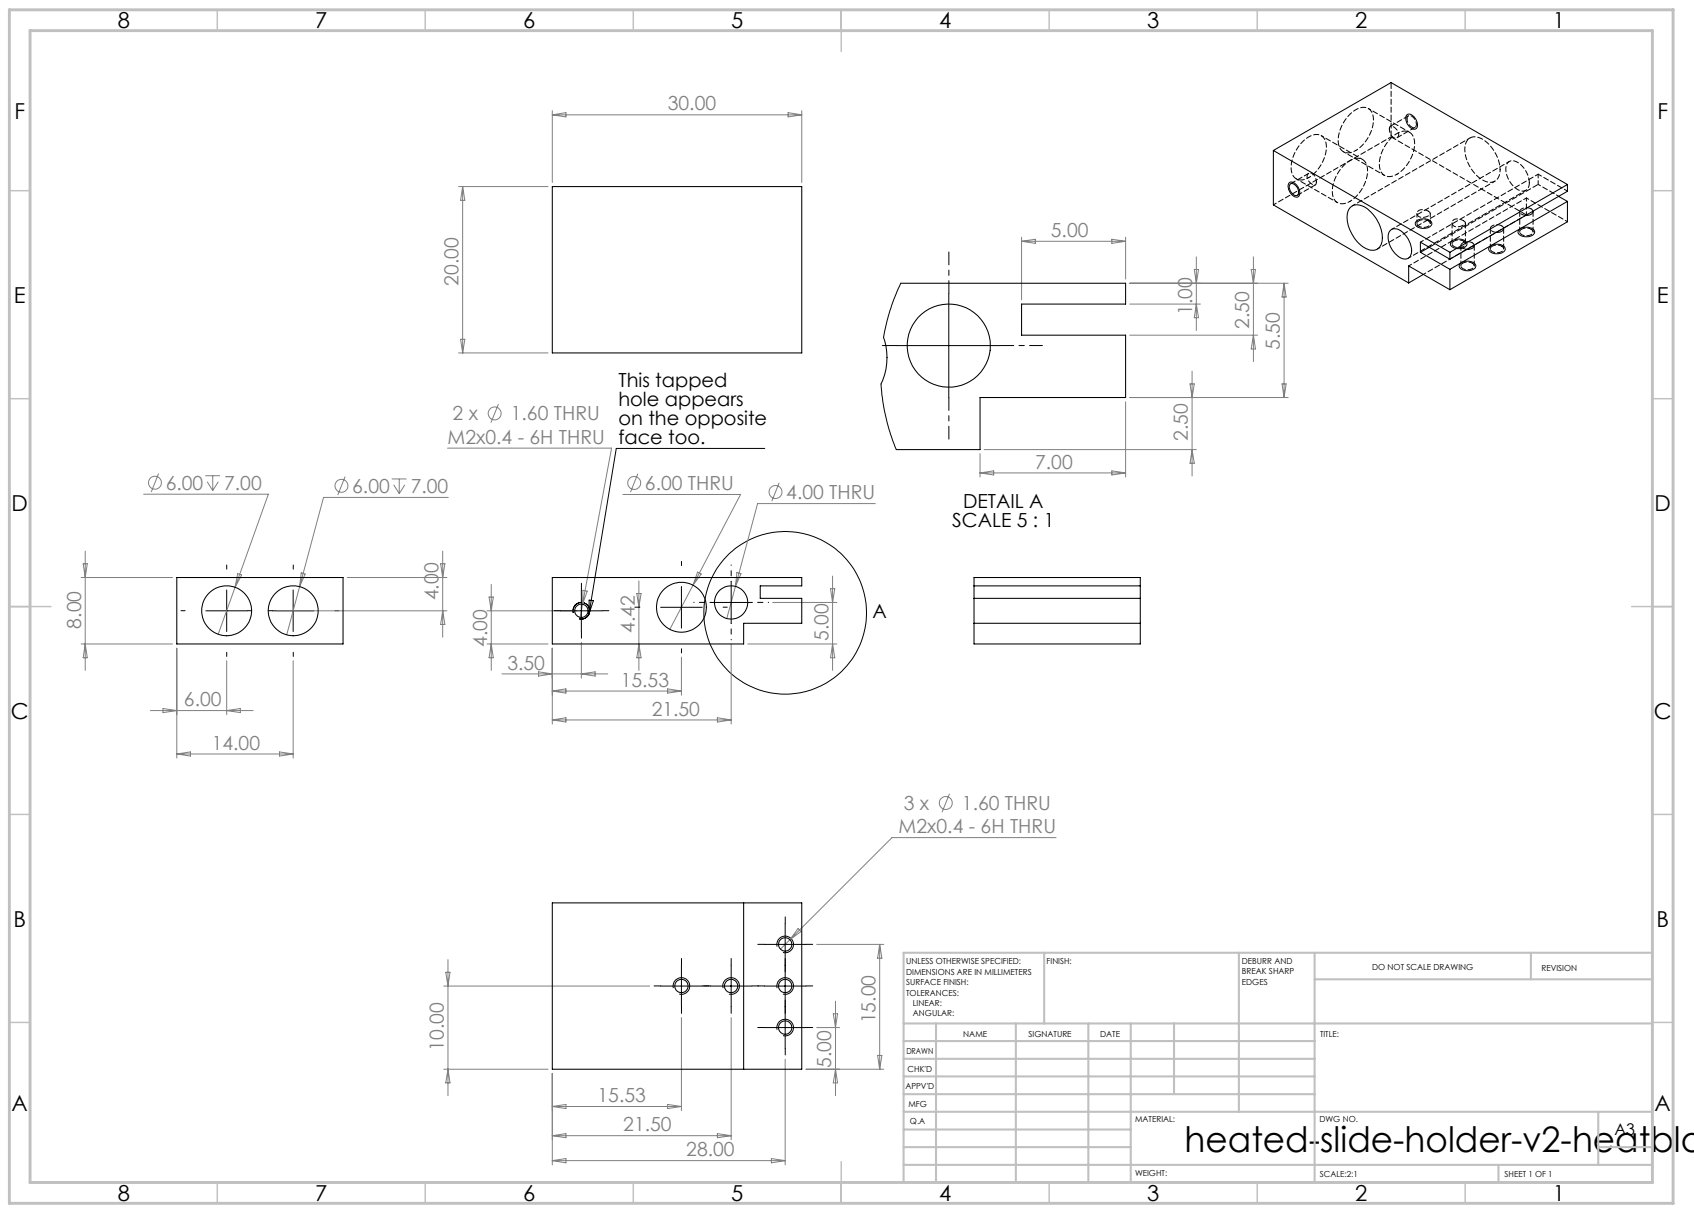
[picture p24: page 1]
1.60 THRU; M2x0.4 - 6H THRU; 6.00 THRU; 4.00 THRU; DETAIL A SCALE 5 : 1; FINISH:; DEBURR AND; BREAK SHARP; DO NOT SCALE DRAWING; REVISION; SCALE:2:1; SHEET 1 OF 1

This tapped
hole appears
on the opposite
face too.

UNLESS OTHERWISE SPECIFIED:
DIMENSIONS ARE IN MILLIMETERS
SURFACE FINISH:
TOLERANCES:
LINEAR:
ANGULAR:

NAME | SIGNATURE | DATE | | | | TITLE:

DRAWN
CHK'D
APPV'D
MFG
Q.A | | | | MATERIAL: | DWG NO. | A3

heated-slide-holder-v2-heatblock

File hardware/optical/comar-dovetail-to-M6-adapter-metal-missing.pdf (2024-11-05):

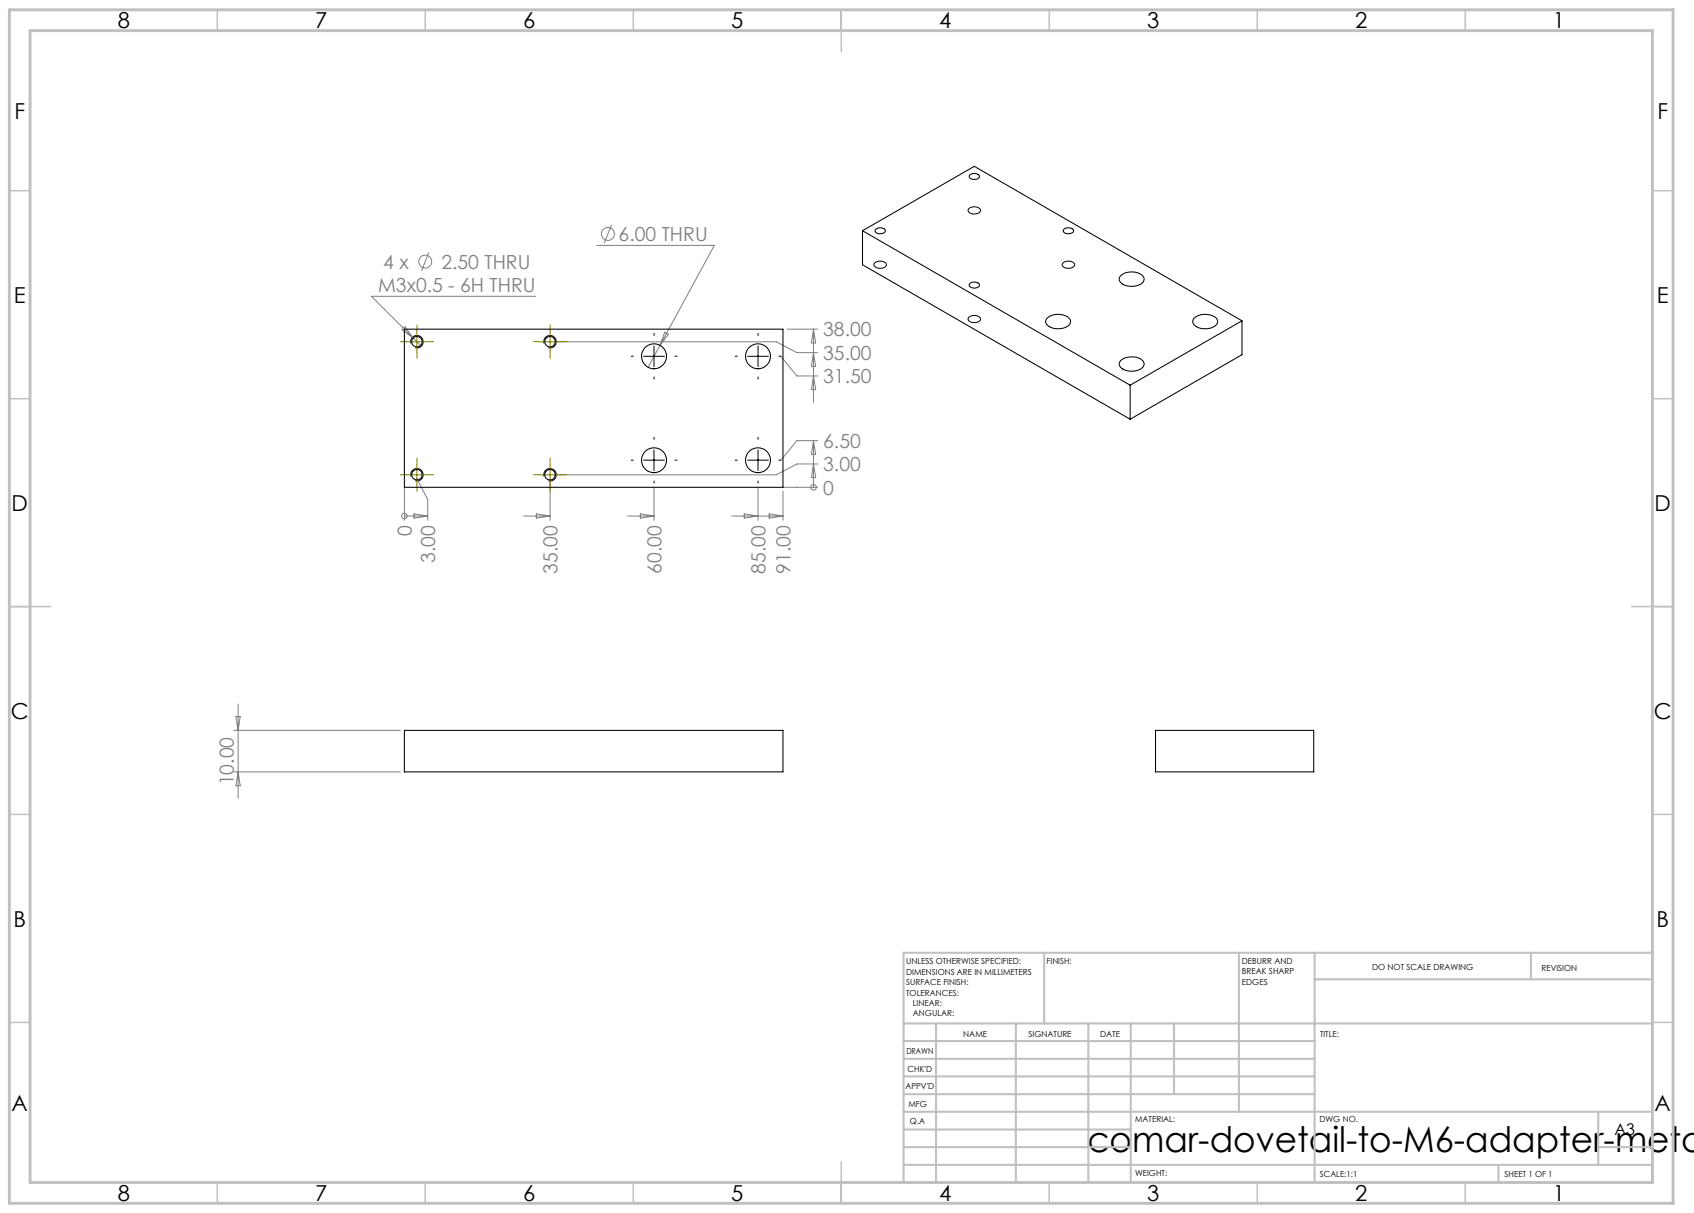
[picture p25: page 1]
2.50 THRU; M3x0.5 - 6H THRU; 6.00 THRU; FINISH:; DEBURR AND; BREAK SHARP; DO NOT SCALE DRAWING; REVISION; SCALE:1:1; SHEET 1 OF 1

UNLESS OTHERWISE SPECIFIED:
DIMENSIONS ARE IN MILLIMETERS
SURFACE FINISH:
TOLERANCES:
LINEAR:
ANGULAR:

NAME | SIGNATURE | DATE | | | | TITLE:

DRAWN
CHK'D
APPV'D
MFG
Q.A | | | | MATERIAL: | DWG NO. | A3

comar-dovetail-to-M6-adapter-metal-missing

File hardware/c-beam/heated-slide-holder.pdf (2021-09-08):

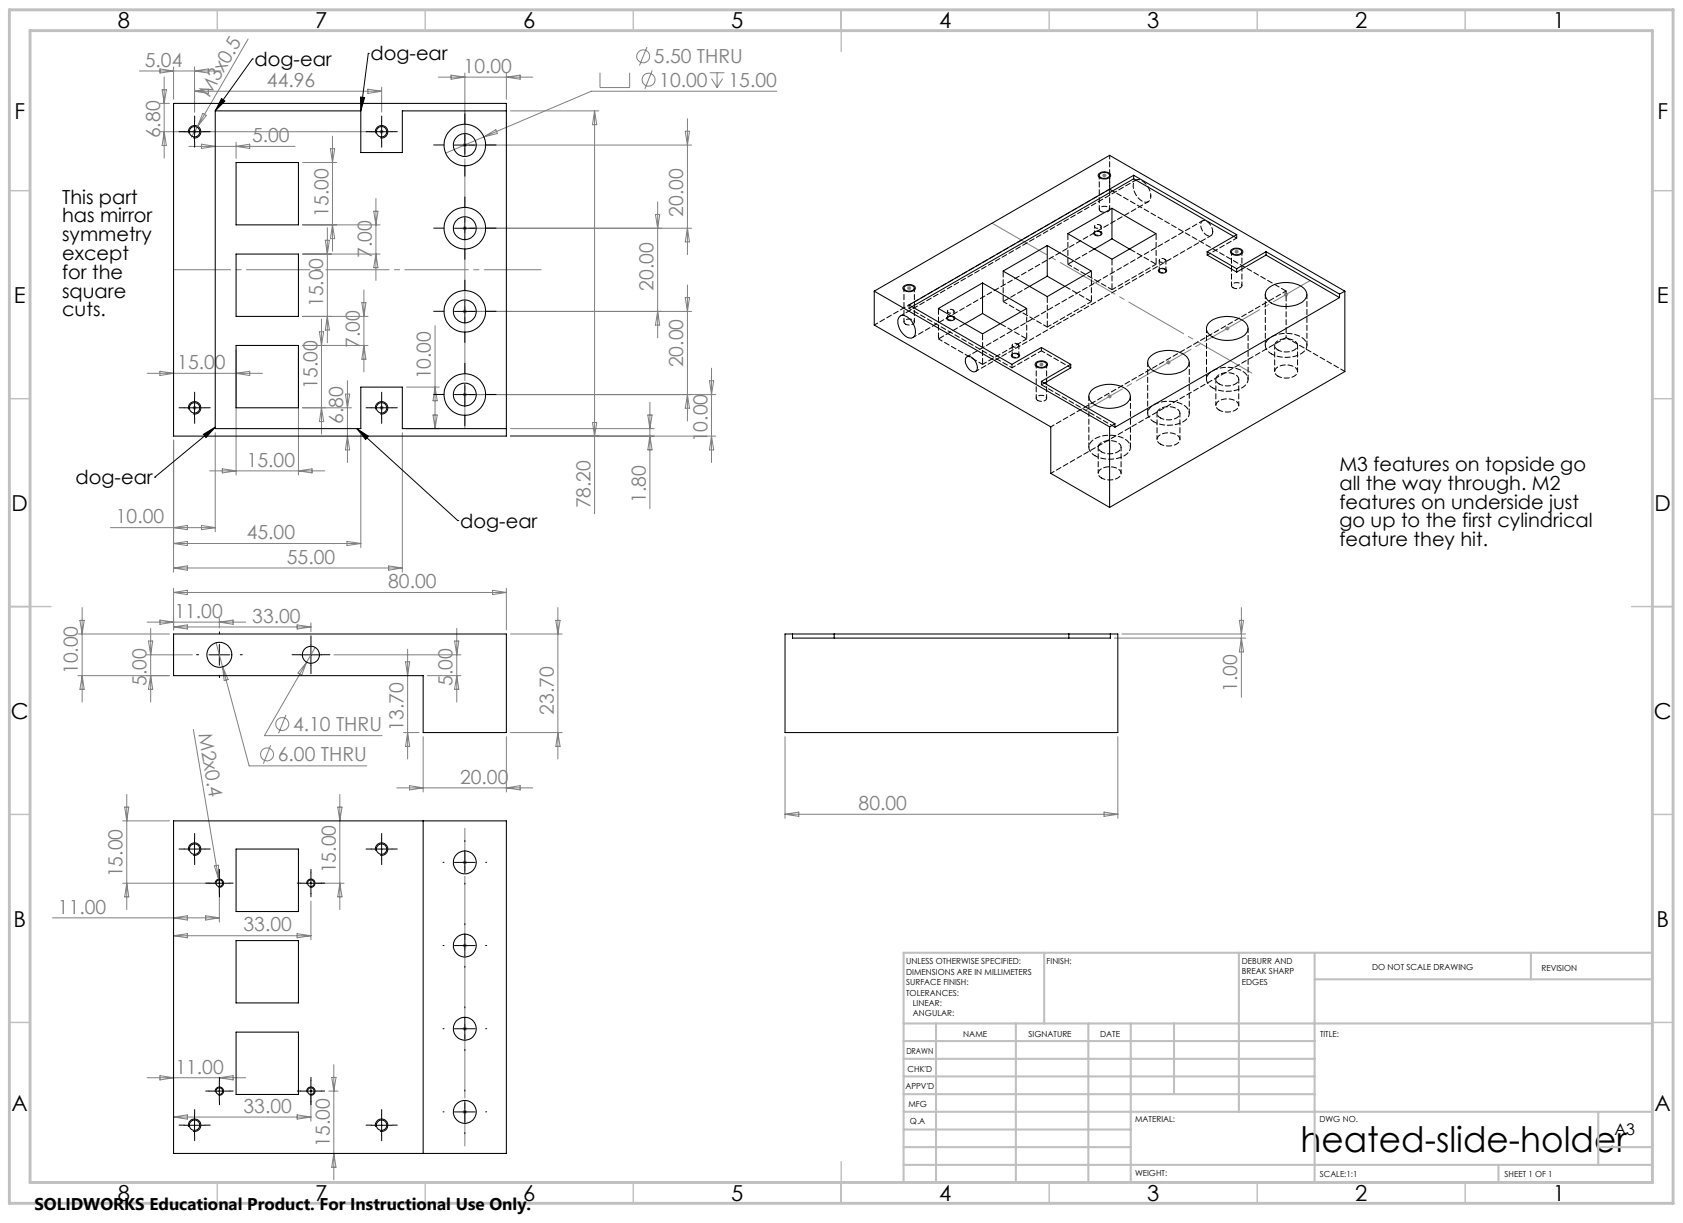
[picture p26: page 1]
6.00 THRU; 4.10 THRU; 5.50 THRU 10.00 15.00; This part has mirror; for the; FINISH:; DEBURR AND; BREAK SHARP; DO NOT SCALE DRAWING; REVISION; SCALE:1:1; SHEET 1 OF 1

M3 features on topside go
all the way through. M2
features on underside just
go up to the first cylindrical
feature they hit.

UNLESS OTHERWISE SPECIFIED:
DIMENSIONS ARE IN MILLIMETERS
SURFACE FINISH:
TOLERANCES:
LINEAR:
ANGULAR:

NAME | SIGNATURE | DATE | | | | TITLE:

DRAWN
CHK'D
APPV'D
MFG
Q.A | | | | MATERIAL: heated-slide-holder | DWG NO. | A3

SOLIDWORKS Educational Product. For Instructional Use Only.

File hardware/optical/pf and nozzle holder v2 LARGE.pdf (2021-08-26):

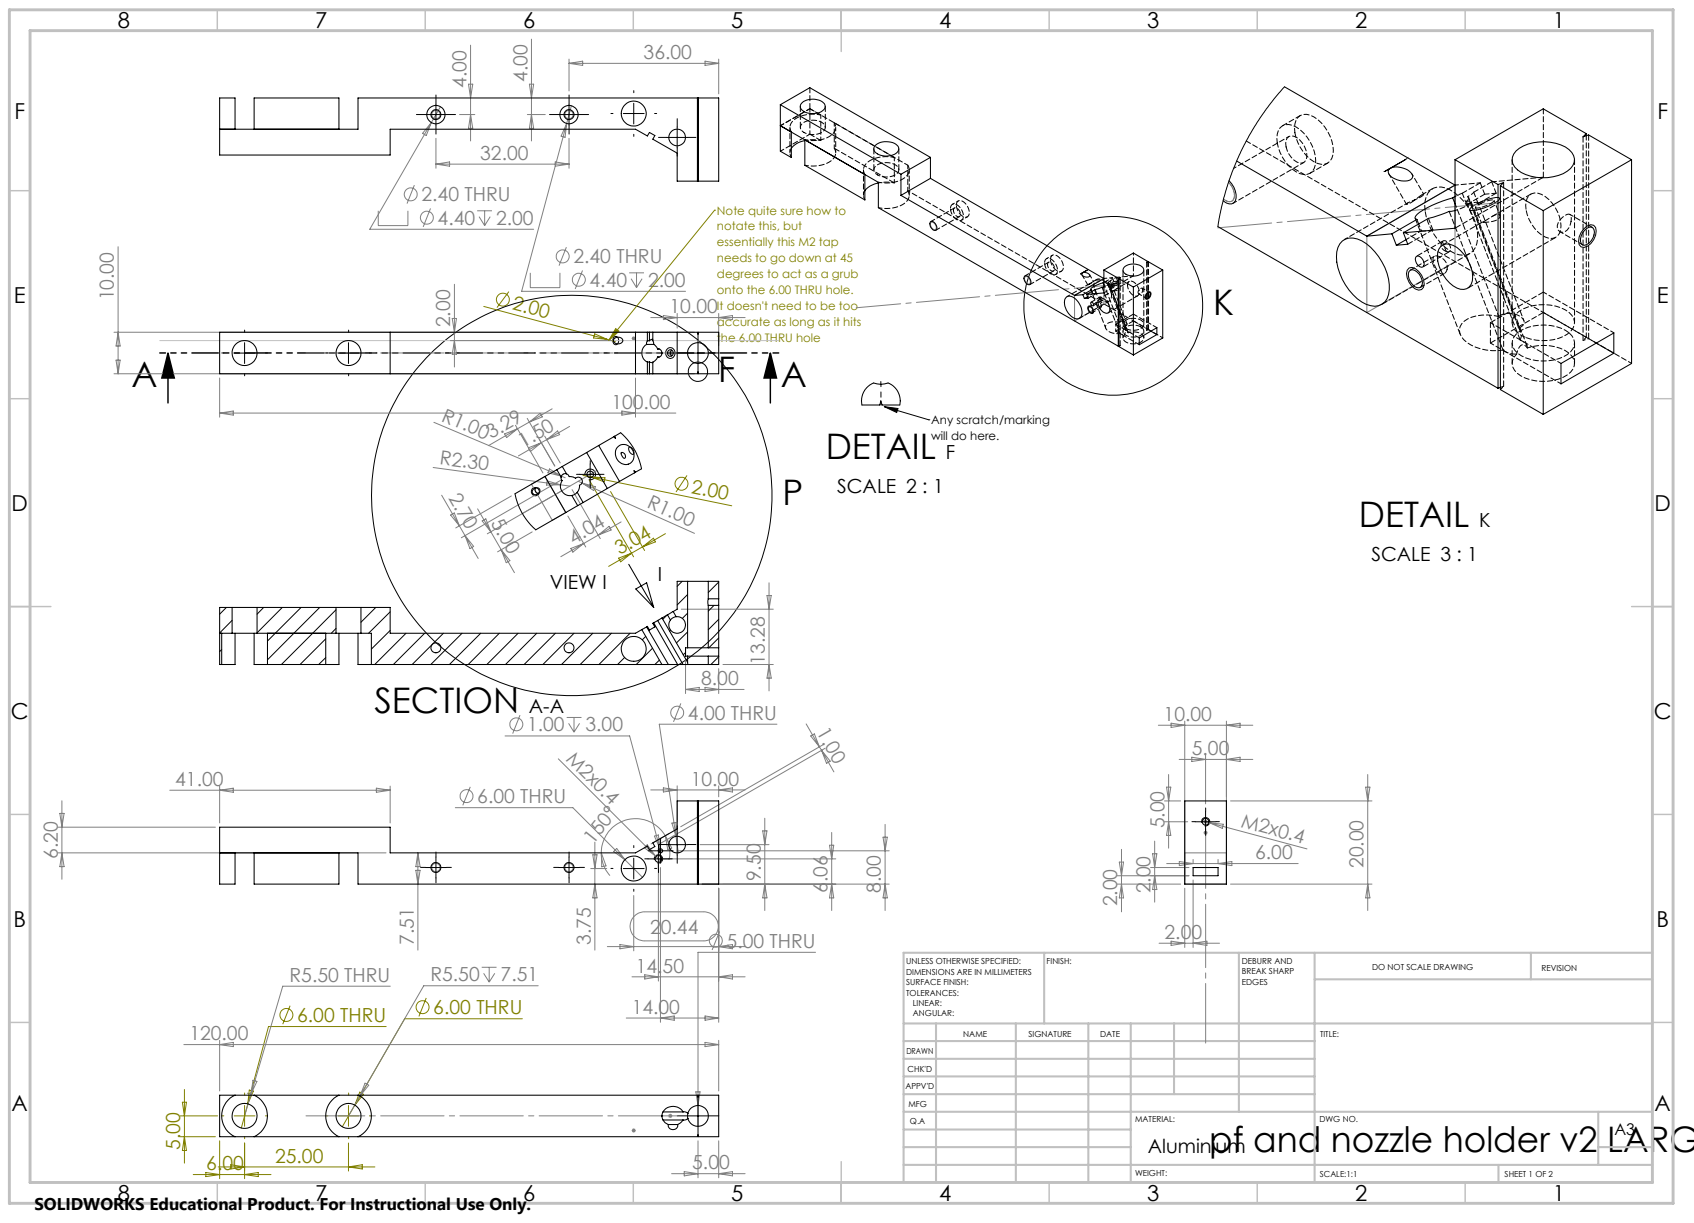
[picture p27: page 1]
4.00 THRU 1.00 3.00; 6.00 THRU; SECTION A-A; 2.40 THRU 4.40 2.00; R5.50 THRU; R5.50 7.51 6.00 THRU; 5.00 THRU; DETAIL F; SCALE 2 : 1; Any scratch/marking; VIEW I; DETAIL K; SCALE 3 : 1; FINISH:; DEBURR AND; BREAK SHARP; DO NOT SCALE DRAWING; REVISION; SCALE:1:1; SHEET 1 OF 2

Note quite sure how to
notate this, but
essentially this M2 tap
needs to go down at 45
degrees to act as a grub
onto the 6.00 THRU hole.
It doesn't need to be too
accurate as long as it hits
the 6.00 THRU hole

will do here. 1.50

UNLESS OTHERWISE SPECIFIED:
DIMENSIONS ARE IN MILLIMETERS
SURFACE FINISH:
TOLERANCES:
LINEAR:
ANGULAR:

NAME | SIGNATURE | DATE | | | | TITLE:

DRAWN
CHK'D
APPV'D
MFG
Q.A | | | | MATERIAL: Aluminium | DWG NO. | A3

SOLIDWORKS Educational Product. For Instructional Use Only.

pf and nozzle holder v2 LARGE

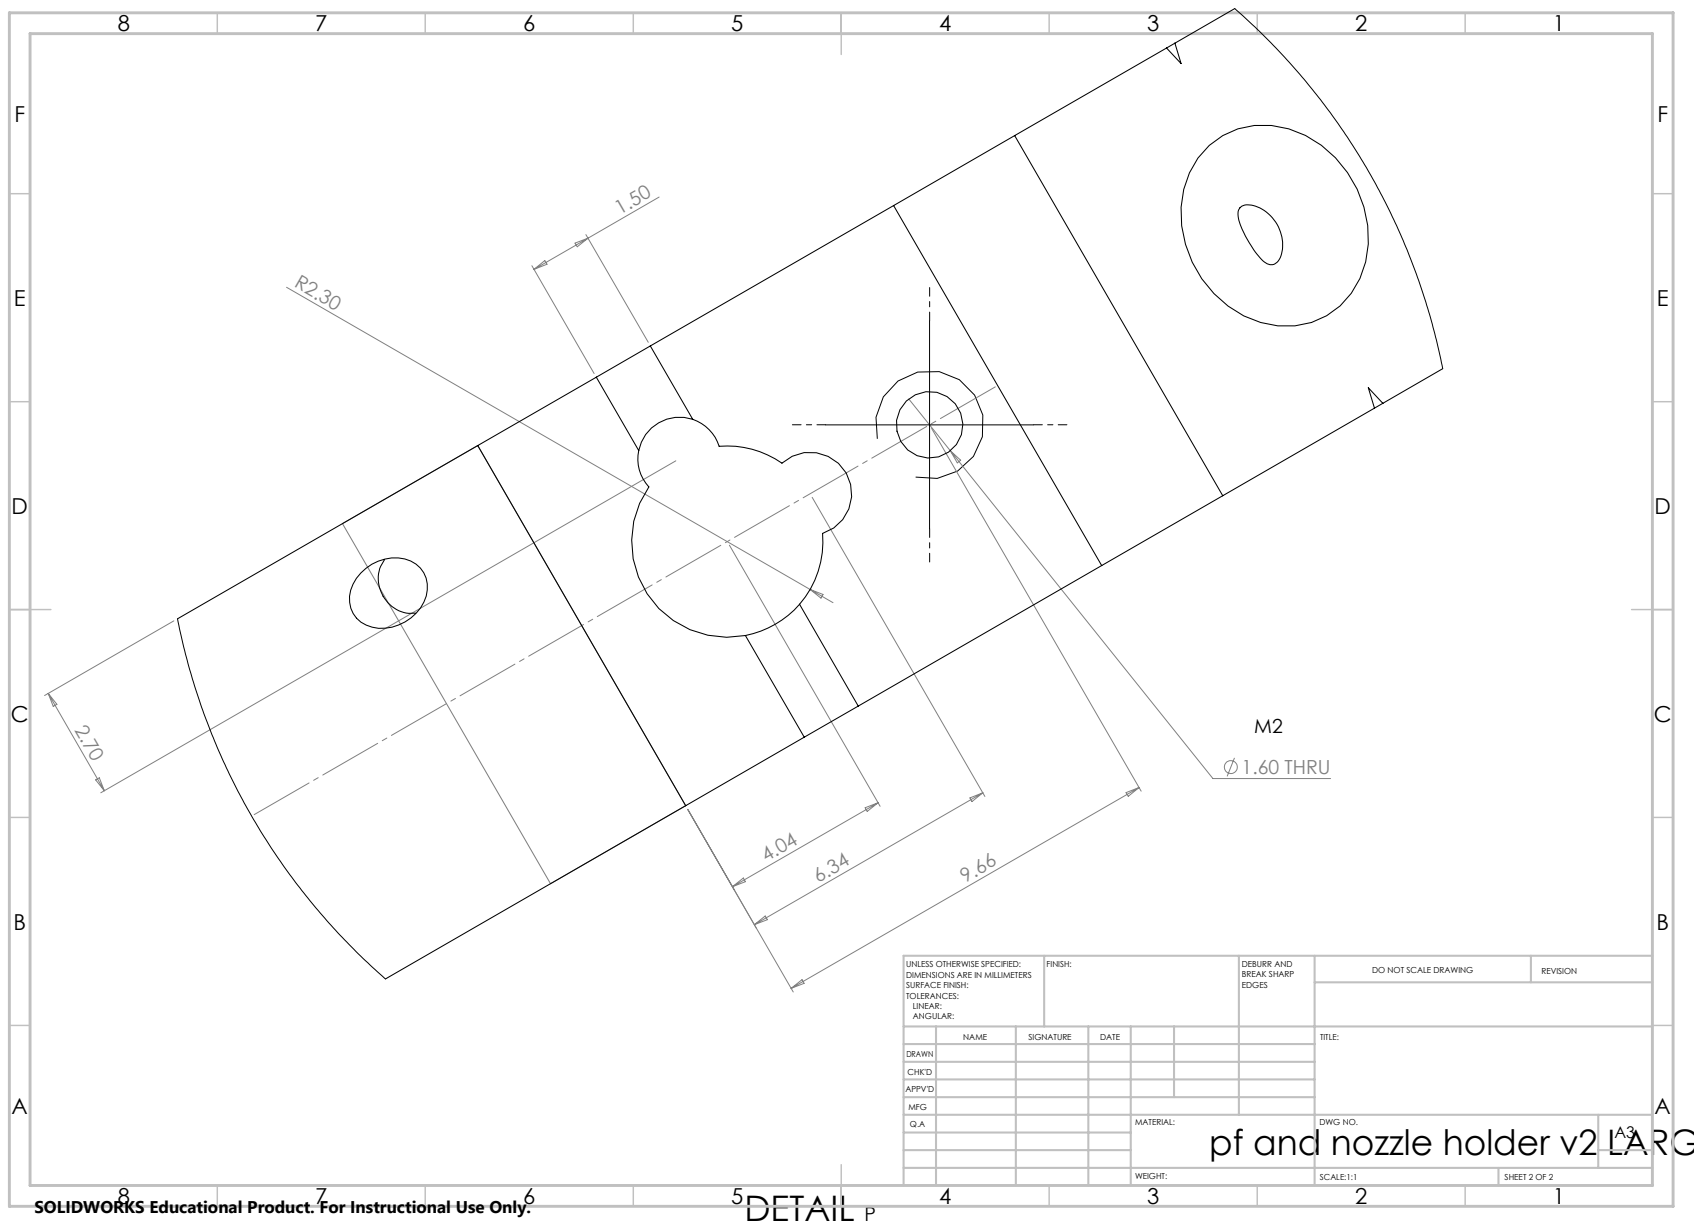
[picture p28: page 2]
1.60 THRU; DETAIL P; FINISH:; DEBURR AND; BREAK SHARP; DO NOT SCALE DRAWING; REVISION; SCALE:1:1; SHEET 2 OF 2

UNLESS OTHERWISE SPECIFIED:
DIMENSIONS ARE IN MILLIMETERS
SURFACE FINISH:
TOLERANCES:
LINEAR:
ANGULAR:

NAME | SIGNATURE | DATE | | | | TITLE:

DRAWN
CHK'D
APPV'D
MFG
Q.A | | | | MATERIAL: | DWG NO. | A3

pf and nozzle holder v2 LARGE

SOLIDWORKS Educational Product. For Instructional Use Only.

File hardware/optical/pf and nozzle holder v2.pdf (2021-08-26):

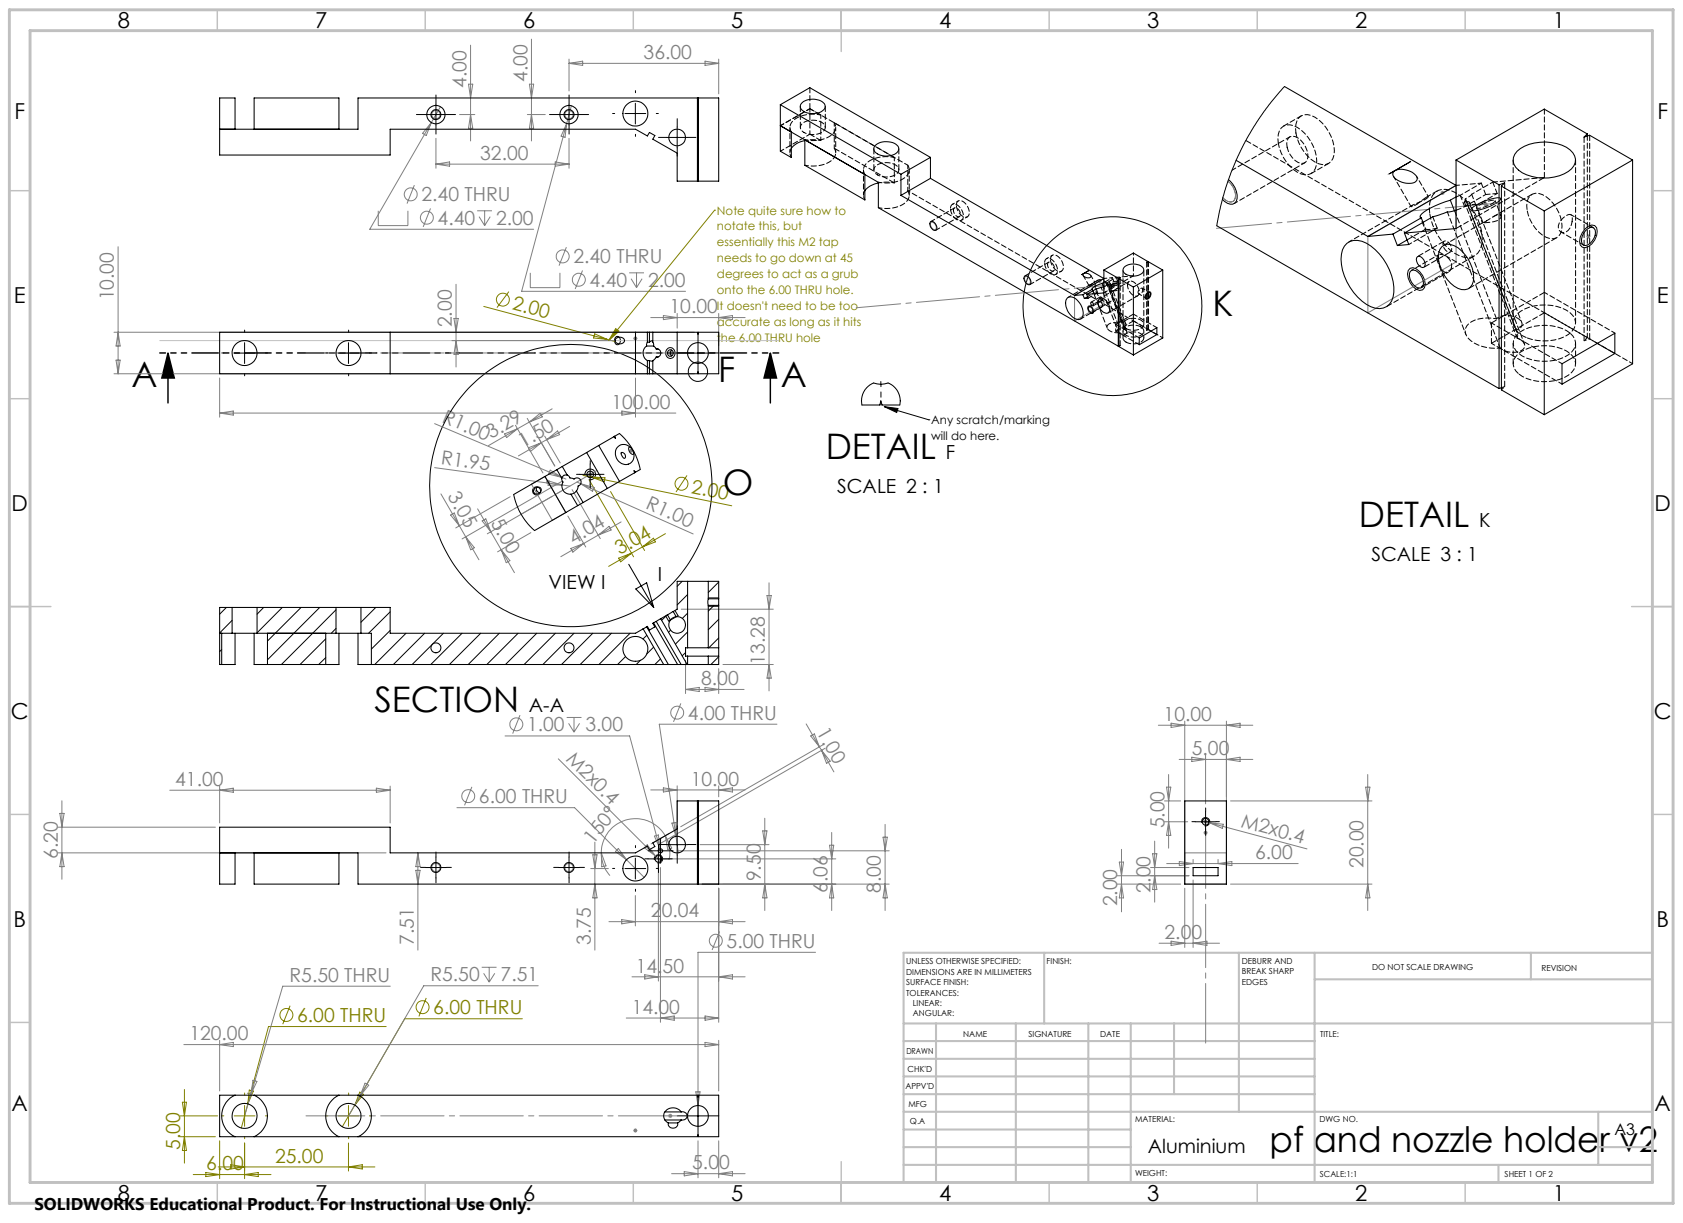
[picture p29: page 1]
4.00 THRU 1.00 3.00; 6.00 THRU; SECTION A-A; 2.40 THRU 4.40 2.00; R5.50 THRU; R5.50 7.51 6.00 THRU; 5.00 THRU; SCALE 2 : 1; VIEW I; DETAIL K; SCALE 3 : 1; FINISH:; DEBURR AND; BREAK SHARP; DO NOT SCALE DRAWING; REVISION; SCALE:1:1; SHEET 1 OF 2

Note quite sure how to
notate this, but
essentially this M2 tap
needs to go down at 45
degrees to act as a grub
onto the 6.00 THRU hole.
It doesn't need to be too
accurate as long as it hits
the 6.00 THRU hole

will do here. 1.50

Any scratch/marking
DETAIL F

UNLESS OTHERWISE SPECIFIED:
DIMENSIONS ARE IN MILLIMETERS
SURFACE FINISH:
TOLERANCES:
LINEAR:
ANGULAR:

NAME | SIGNATURE | DATE | | | | TITLE:

DRAWN
CHK'D
APPV'D
MFG
Q.A | | | | MATERIAL: pf and nozzle holder v2 Aluminium | DWG NO. | A3

SOLIDWORKS Educational Product. For Instructional Use Only.

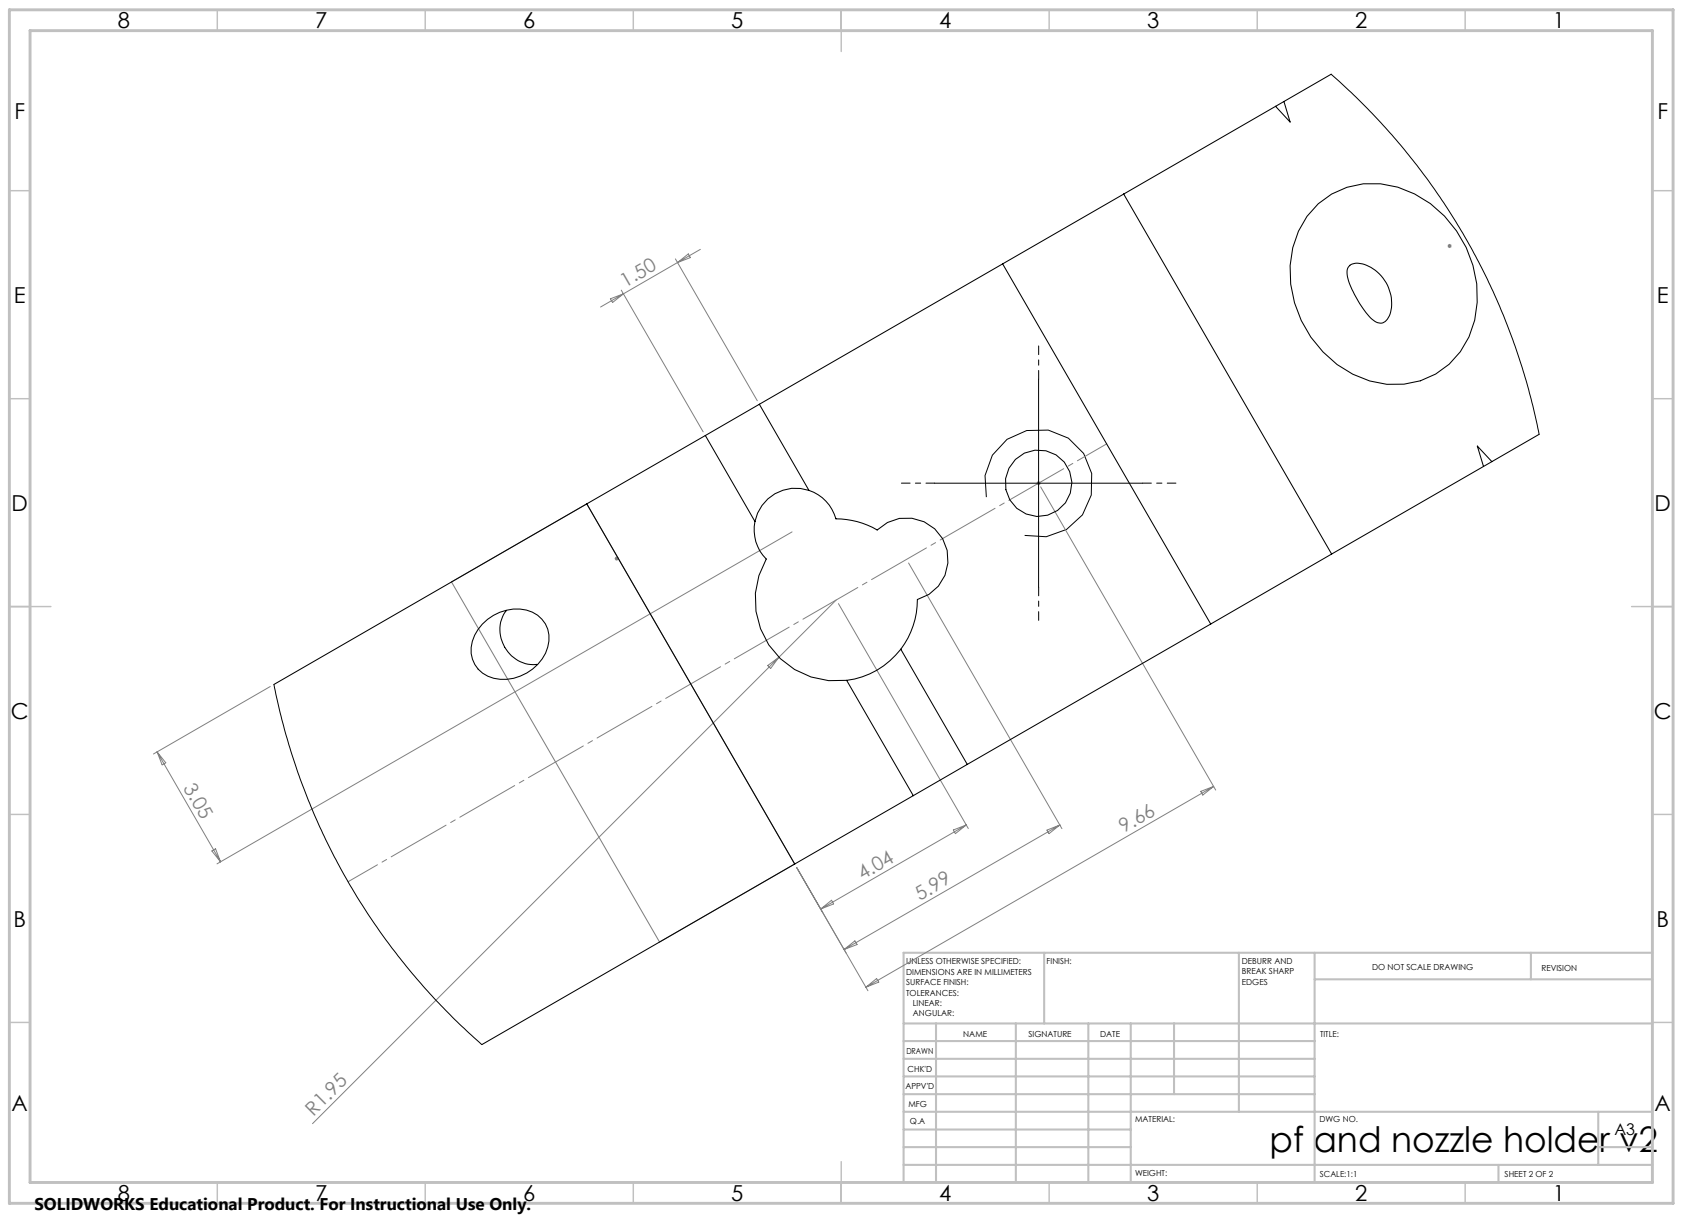
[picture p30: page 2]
FINISH:; DEBURR AND; BREAK SHARP; DO NOT SCALE DRAWING; REVISION; SCALE:1:1; SHEET 2 OF 2

UNLESS OTHERWISE SPECIFIED:
DIMENSIONS ARE IN MILLIMETERS
SURFACE FINISH:
TOLERANCES:
LINEAR:
ANGULAR:

NAME | SIGNATURE | DATE | | | | TITLE:

DRAWN
CHK'D
APPV'D
MFG
Q.A | | | | MATERIAL: pf and nozzle holder v2 | DWG NO. | A3

SOLIDWORKS Educational Product. For Instructional Use Only.

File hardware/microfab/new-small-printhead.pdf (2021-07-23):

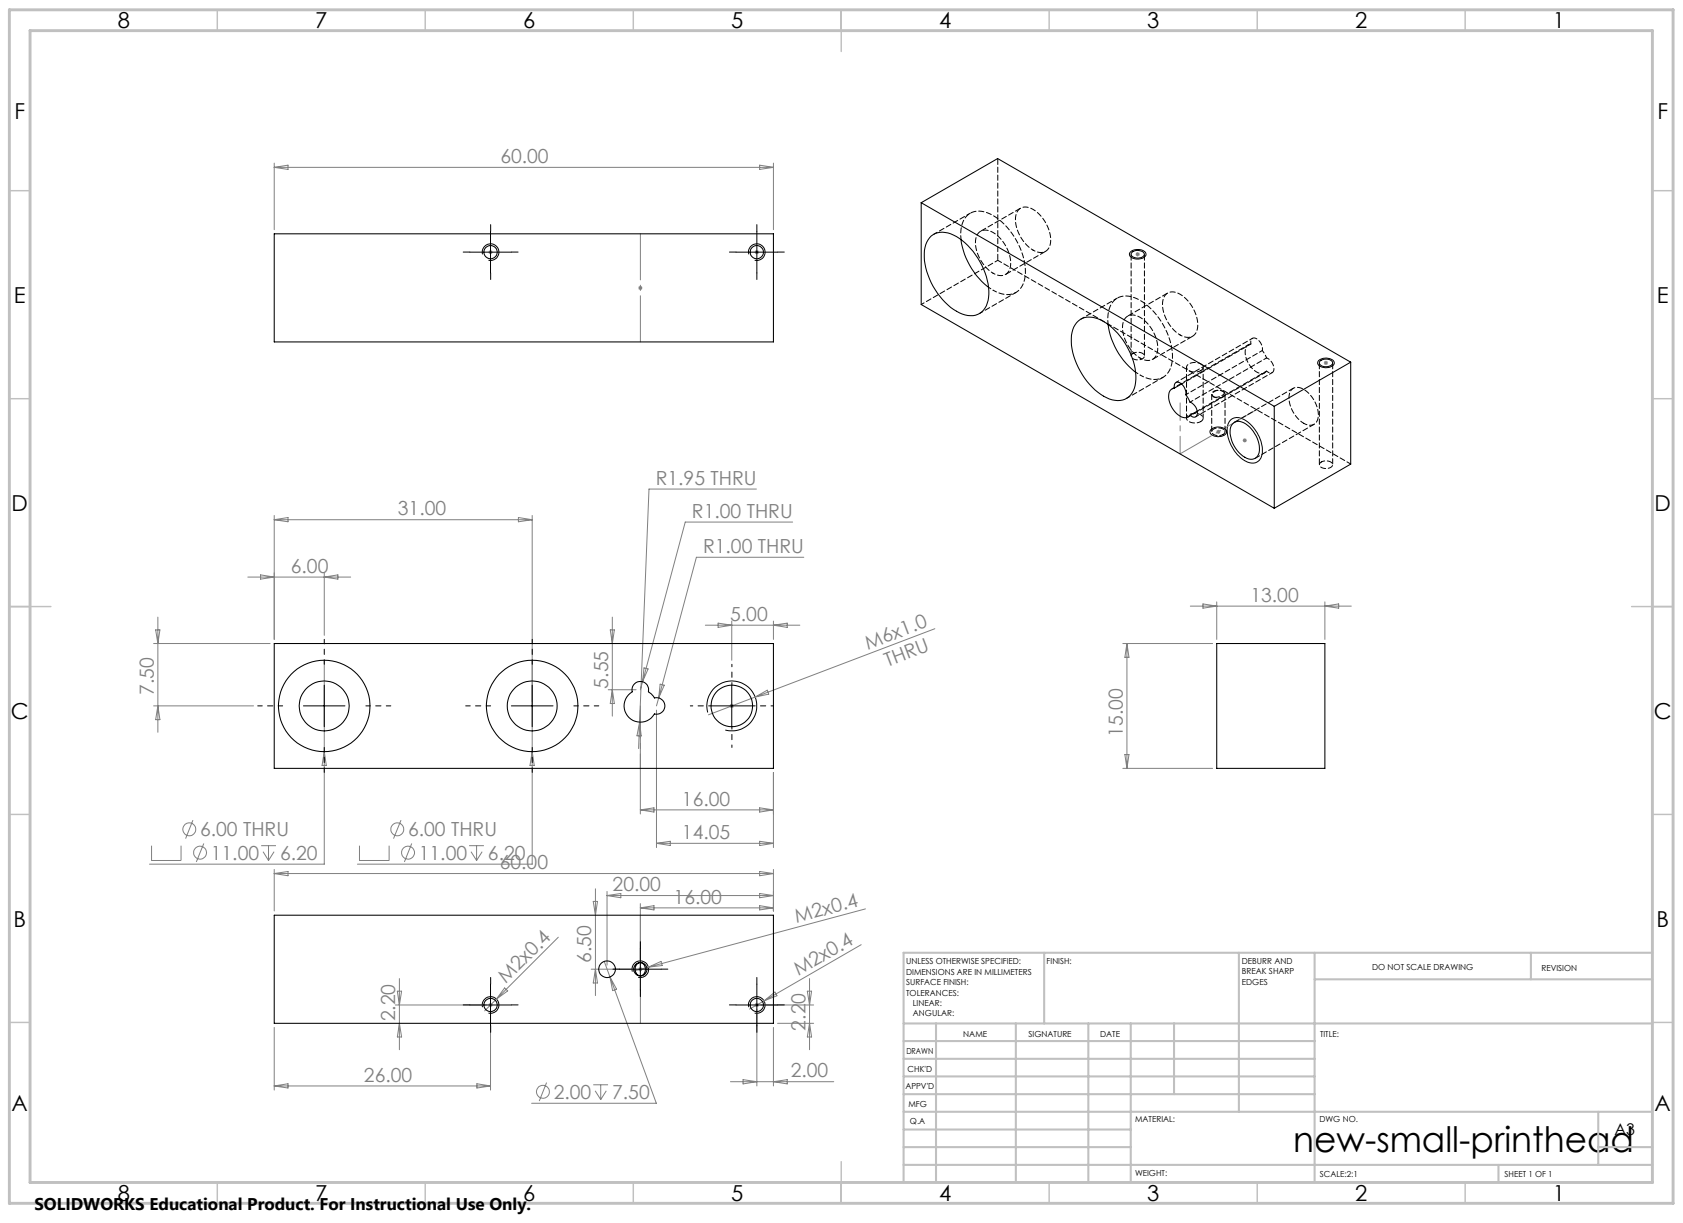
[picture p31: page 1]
R1.95 THRU; R1.00 THRU; 6.00 THRU 11.00 6.20; FINISH:; DEBURR AND; BREAK SHARP; DO NOT SCALE DRAWING; REVISION; SCALE:2:1; SHEET 1 OF 1

UNLESS OTHERWISE SPECIFIED:
DIMENSIONS ARE IN MILLIMETERS
SURFACE FINISH:
TOLERANCES:
LINEAR:
ANGULAR:

NAME | SIGNATURE | DATE | | | | TITLE:

DRAWN
CHK'D
APPV'D
MFG
Q.A | | | | MATERIAL: new-small-printhead | DWG NO. | A3

SOLIDWORKS Educational Product. For Instructional Use Only.

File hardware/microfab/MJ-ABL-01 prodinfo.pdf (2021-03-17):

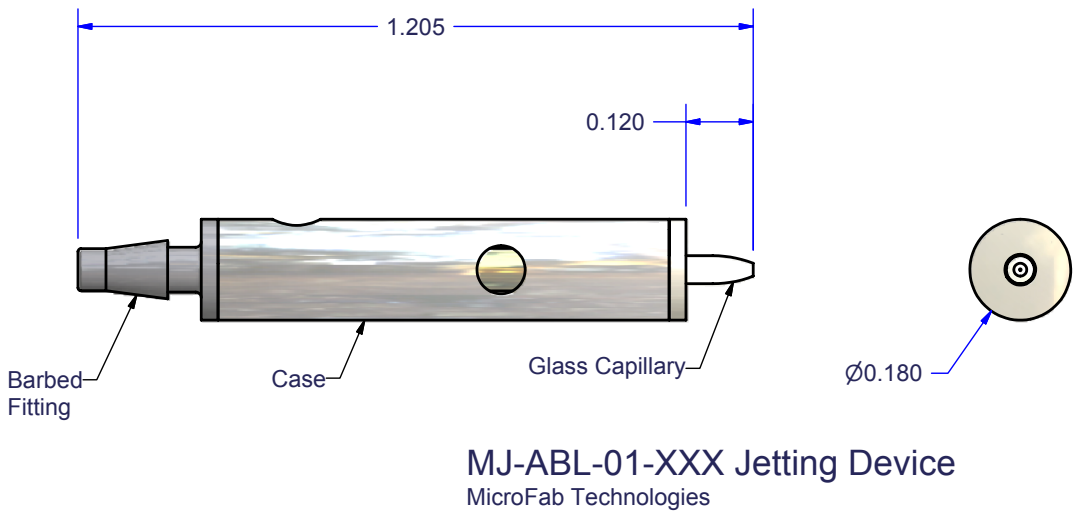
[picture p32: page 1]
Barbed Fitting; Case; Glass Capillary

MJ-ABL-01-XXX Jetting Device
MicroFab Technologies

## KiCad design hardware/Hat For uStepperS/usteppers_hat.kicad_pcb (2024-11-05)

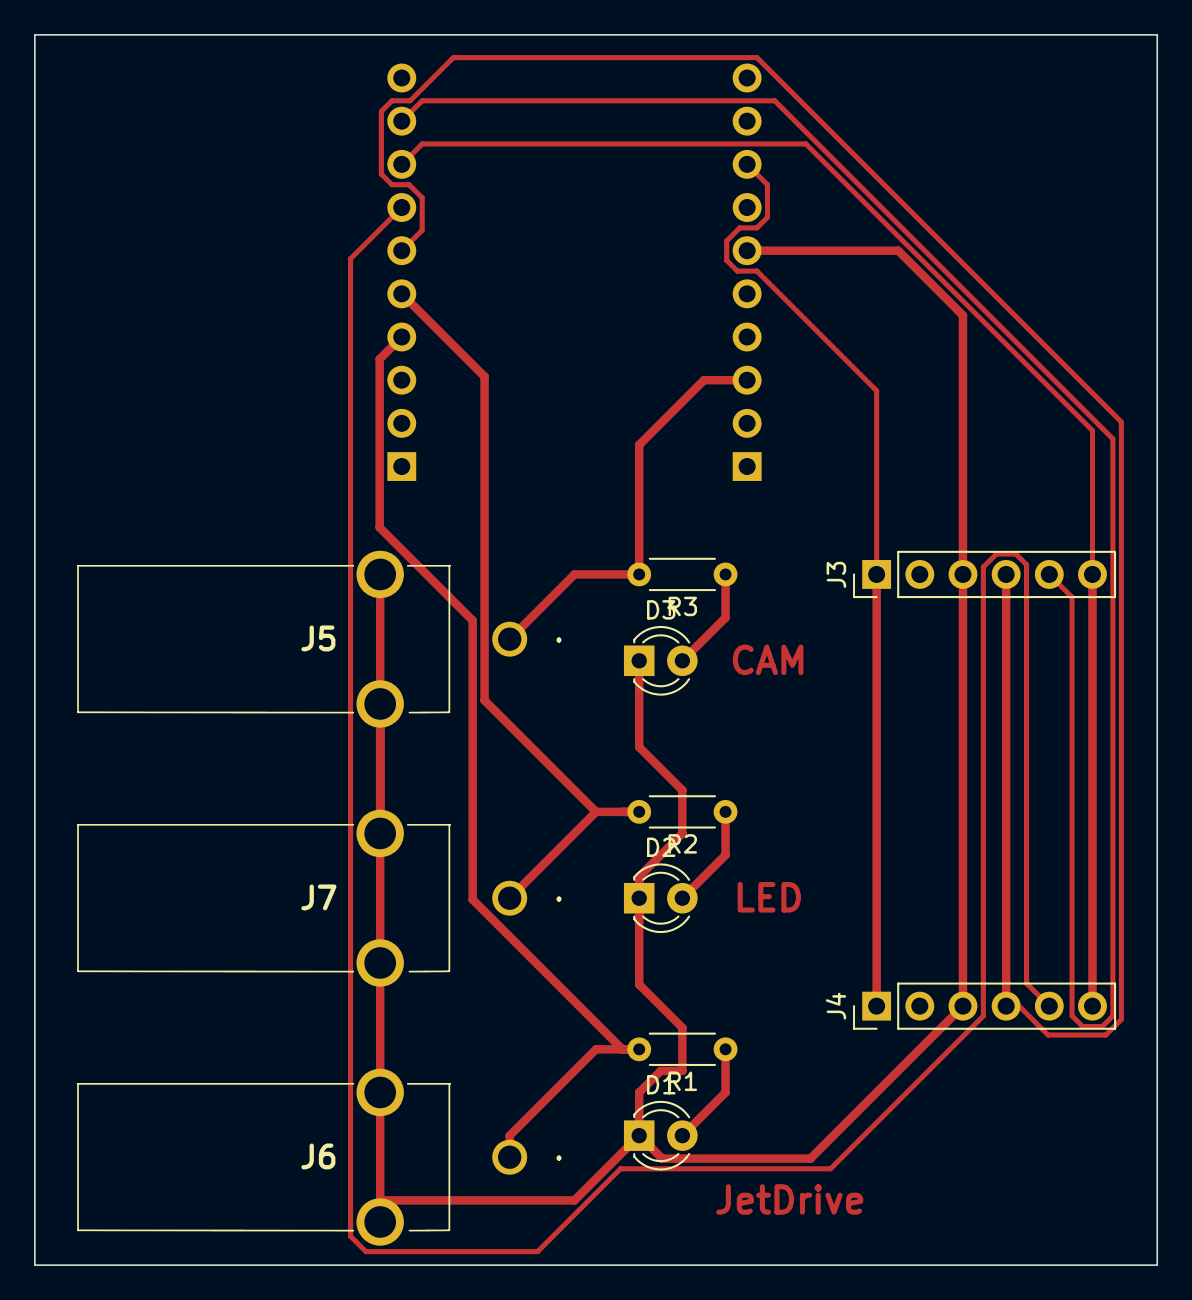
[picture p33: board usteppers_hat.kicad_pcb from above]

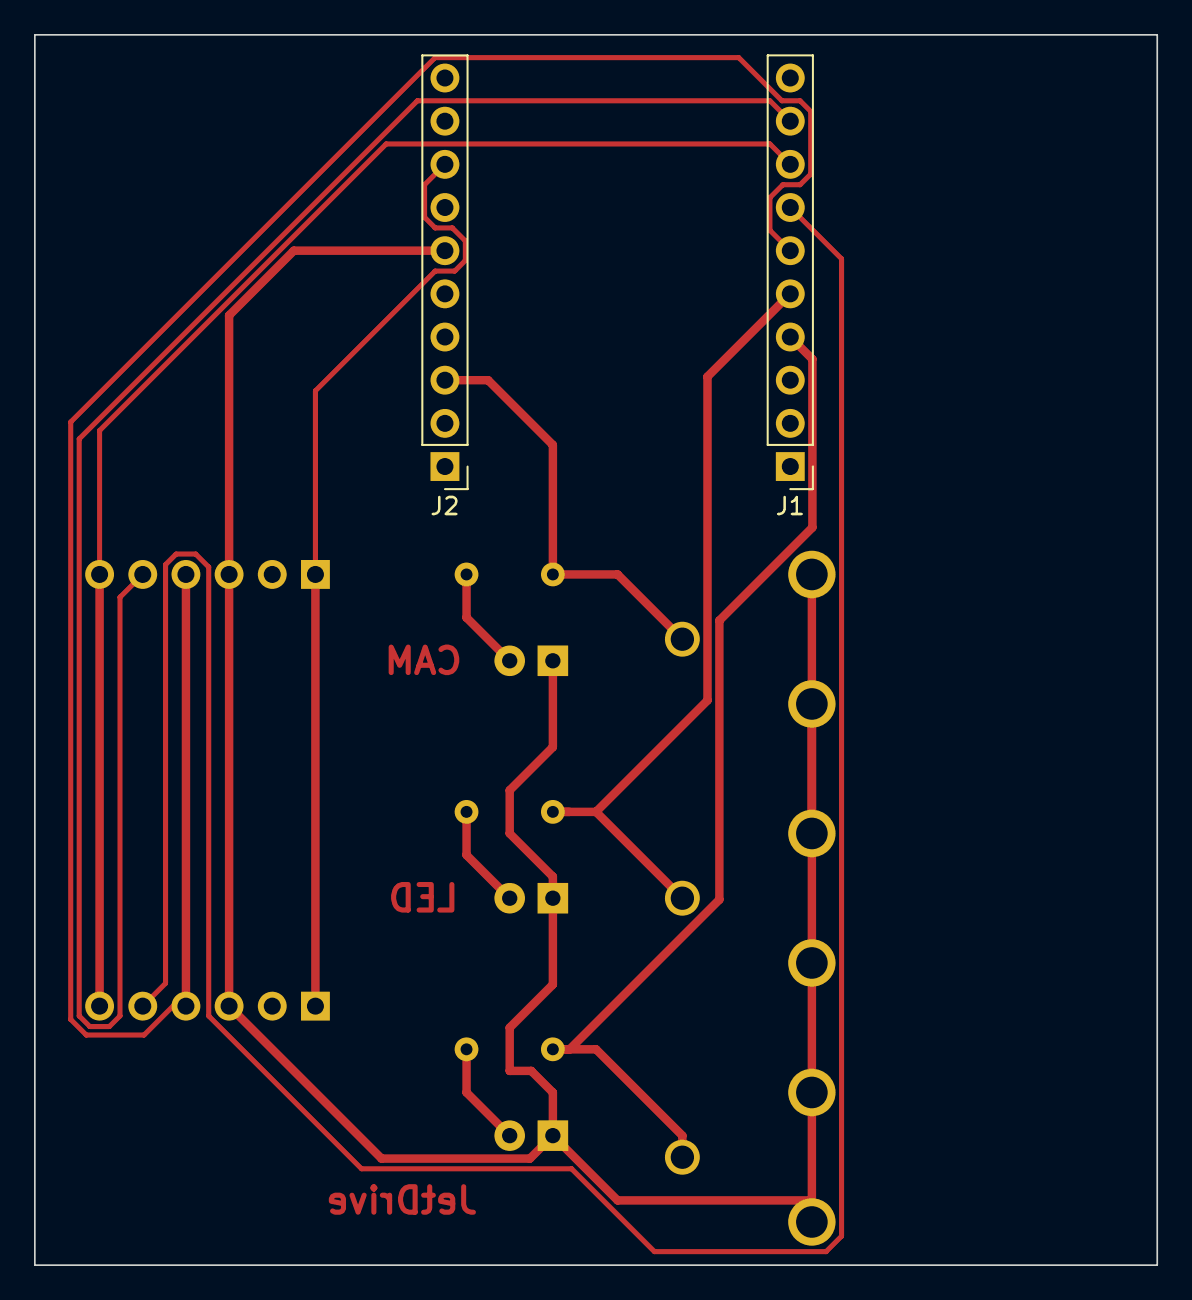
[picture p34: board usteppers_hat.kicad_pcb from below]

Board: 2 copper layers, 66.0 x 72.4 mm, 13 parts (2 on the bottom side), 13 nets.

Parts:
D1, D2, D3: LED; LED_D3.0mm
J1, J2: Conn_01x10_Male; PinHeader_1x10_P2.54mm_Vertical
J3, J4: Conn_01x06_Female; PinHeader_1x06_P2.54mm_Vertical
J5, J6, J7: 5414373-1; 54143731
R1, R2, R3: 330; R_Axial_DIN0204_L3.6mm_D1.6mm_P5.08mm_Horizontal

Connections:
/5V: J2.8, J3.1, J4.1
/A0: J2.3, J5.1, R3.2
/CLK: J1.8, J3.6, J4.6
/CS1: J1.7, J4.5
/CS2: J1.9, J3.5
/D3: J1.4, J6.1, R1.2
/D4: J1.5, J7.1, R2.2
/D5: J1.6, J3.4, J4.4
/VIN: J2.4, J2.5
Earth: D1.1, D2.1, D3.1, J1.10, J2.6, J2.7, J3.3, J4.3, J5.2, J5.3, J6.2, J6.3, J7.2, J7.3
unnamed: D1.2, R1.1
unnamed: D2.2, R2.1
unnamed: D3.2, R3.1

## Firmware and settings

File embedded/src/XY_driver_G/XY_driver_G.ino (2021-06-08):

#include <uStepperS.h>
#include "gcode.h"
#include "constants.h"

#include <SPI.h>
#include "Adafruit_MAX31855.h"


#define UARTPORT Serial
#define DEBUGPORT Serial1

#define ANGLE_DEADZONE 0.5

uStepperS stepper;
GCode comm;

//thermocouples

Adafruit_MAX31855 thermocouple(MAXCLK, MAXCS, MAXDO); 
Adafruit_MAX31855 thermocouple2(MAXCLK, MAXCS2, MAXDO);

float target = 0.0;
bool targetReached = true;

int triggerSeq = 0;
int maxTriggerSeq = 4;

volatile bool frameLockout = false;
unsigned long nextFrame = 0;

// Used to keep track of configuration
struct
{
  float acceleration = 2000.0; // In steps/s
  float velocity = 200.0;      // In steps/s = 60 RPM
  uint8_t brake = COOLBRAKE;
  boolean closedLoop = false;
  float homeVelocity = 40.0; // In rpm
  int8_t homeThreshold = 4;
  bool homeDirection = CW; // In rpm
  uint32_t LEDPulseLengthMicros = 20;
  uint32_t LEDDelayMicros = 40;
  uint32_t LEDSecondMicros = 40;

  int LEDDelayTimerStart = 65064;  //value the timer stats at to count up to 65536.
  int LEDPulseTimerStart = 65264;  //value the timer stats at to count up to 65536. this value is abous 20us
  int LEDSecondTimerStart = 65264; // same but for the second pulse
  float cameraMaxFPS = 30;
  long cameraMinFrameTime = 33; //Camera Lockout time in milliseconds. by default this corresponds to 30 FPS

  bool secondPulseEnabled = false;

  float progAngleOffset = 0;
  float progAnglePeriod = 10;
  bool progressiveModeEnabled = false;

  float continuousFrequency = 5;
  int continuousOCR = 12500;
  bool continuousModeEnabled = false;

} conf;

//timer toggle stuff



void setup()
{

  //set up the trigger out ports as outputs, low.

  //start the serial interface

  UARTPORT.begin(115200);






  //configure the stepper motor

  stepper.setup();

  //DDRB |= (1 << 4);
  DDRB &= ~(1<<4); //clear bit 4 of DDRB, undoing a bug in uStepperS.

  stepper.setMaxAcceleration(conf.acceleration);
  stepper.setMaxDeceleration(conf.acceleration);
  stepper.setMaxVelocity(conf.velocity);

  // wait for MAX chip to stabilize
  delay(500);
  thermocouple.begin();
  thermocouple2.begin();
  

  configureComm();
  configurePinsAndInterrupts();

}

void configureComm(){
  
  comm.setSendFunc(&uart_send);

  // Add GCode commands
  comm.addCommand(GCODE_MOVE, &uart_move);
  comm.addCommand(GCODE_MOVETO, &uart_moveto);
  comm.addCommand(GCODE_CONTINUOUS, &uart_continuous);
  comm.addCommand(GCODE_BRAKE, &uart_continuous);
  comm.addCommand(GCODE_HOME, &uart_home);

  comm.addCommand(GCODE_STOP, &uart_stop);
  comm.addCommand(GCODE_SET_SPEED, &uart_config);
  comm.addCommand(GCODE_SET_ACCEL, &uart_config);
  comm.addCommand(GCODE_SET_BRAKE_FREE, &uart_setbrake);
  comm.addCommand(GCODE_SET_BRAKE_COOL, &uart_setbrake);
  comm.addCommand(GCODE_SET_BRAKE_HARD, &uart_setbrake);
  comm.addCommand(GCODE_SET_CL_ENABLE, &uart_setClosedLoop);
  comm.addCommand(GCODE_SET_CL_DISABLE, &uart_setClosedLoop);

  comm.addCommand(GCODE_RECORD_START, &uart_record);
  comm.addCommand(GCODE_RECORD_STOP, &uart_record);
  comm.addCommand(GCODE_RECORD_ADD, &uart_record);
  comm.addCommand(GCODE_RECORD_PLAY, &uart_record);
  comm.addCommand(GCODE_RECORD_PAUSE, &uart_record);

  comm.addCommand(GCODE_REQUEST_DATA, &uart_sendData);
  comm.addCommand(GCODE_REQUEST_CONFIG, &uart_sendConfig);
  comm.addCommand(GCODE_REQUEST_TEMP, &uart_sendTemp);

  comm.addCommand(GCODE_TRIGGER, &uart_trigger);
  comm.addCommand(GCODE_TRIGGER_ALT, &uart_trigger);
  comm.addCommand(GCODE_CONFIGURE_TRIGGER_TIMING, &uart_configureTriggerTiming);
  comm.addCommand(GCODE_CONFIGURE_TRIGGER_PROGRESSIVE, &uart_configureTriggerProgressive);
  comm.addCommand(GCODE_CONFIGURE_TRIGGER_CONTINUOUS, &uart_configureTriggerContinuous);

  // Called if the packet and checksum is ok, but the command is unsupported
  comm.addCommand(NULL, uart_default);

  // Show list off all commands
  // comm.printCommands();
}

void configurePinsAndInterrupts(){

  // initialize timer3 - based on code from http://www.letsmakerobots.com/node/28278

  noInterrupts(); // disable all interrupts
  TCCR3A = 0;
  TCCR3B = 0;
  TCNT3 = 0;
  OCR3A = conf.LEDDelayTimerStart; // preload timer 65536-16MHz*period
  TCCR3B |= (1 << CS30);           // this is a very fast toggle so we don't need a prescaler. ie presacler = 1
  TIMSK3 |= 0;                     //disable ovf interrupt
  //TIMSK3 |= (1 << TOIE3);   // enable timer overflow interrupt

  //initialise timer4 for continuous mode at 5Hz
  TCCR4A = 0;
  TCCR4B = 0;
  TCNT4 = 0;

  OCR4A = conf.continuousOCR; // compare match register 16MHz/256/5Hz
  TCCR4B |= (1 << WGM12);     // CTC mode
  TCCR4B |= (1 << CS12);      // 256 prescaler
  TIMSK4 |= (1 << OCIE1A);    // enable timer compare interrupt

  //Configure Pin Change Interrupts on Digital Pin 2
  //We don't use EXINTs or attachInterrupt because they interact weirdly with the uStepper board.
  //The pin layout here is confusing
  //On the PCB, the pin used is Pin 2.
  //In AVR-land this is PD3 (third bit on Port D).
  //In ISR land, this is PCINT19 - the 19th pin to support PCINT, living on the 2nd bank of PCINTs

  pinMode(2, INPUT_PULLUP); //Make Pin 2 an input

  PCMSK2 |= (1 << 3); //activate PCINT19 aka PD3 aka Pin 2 on the Pin Change Mask 2

  PCICR |= (1 << PCIE2); //Enable PCINT interrupts on bank 2

  //attachInterrupt(digitalPinToInterrupt(2),trigger,FALLING);

  DDR_TRIGGER_LED |= (1 << PIN_TRIGGER_LED);
  DDR_TRIGGER_DROP |= (1 << PIN_TRIGGER_DROP);
  DDR_TRIGGER_SHUTTER |= (1 << PIN_TRIGGER_SHUTTER);
  PORT_TRIGGER_DROP &= ~(1 << PIN_TRIGGER_DROP);
  PORT_TRIGGER_LED &= ~(1 << PIN_TRIGGER_LED);

  interrupts(); // enable all interrupts
}

void handleLockout()
{
  if (frameLockout)
  {
    if (millis() > nextFrame)
    {
      frameLockout = false;
    }
  }
}

//ISR routine for pin 2.
ISR(PCINT2_vect)
{
  bool edge = digitalRead(2);
  //Serial.println(edge);
  if (edge)
  { //check if it was a rising edge
    trigger();
  }                      //if it was, trigger the drop
  EIFR &= ~(1 << INTF0); //Clear interrupt flag
}

ISR(TIMER4_COMPA_vect) // timer compare interrupt service routine

{
  if (conf.continuousModeEnabled)
  {
    trigger();
  }
}

//ISR for the trigger

ISR(TIMER3_OVF_vect)
{
  switch (triggerSeq)
  {
  case 0:
    TCNT3 = conf.LEDDelayTimerStart;
    //digitalWrite(PIN_TRIGGER_DROP, HIGH); //go high
    PORT_TRIGGER_DROP |= (1 << PIN_TRIGGER_DROP);

    break;

  case 1:
    TCNT3 = conf.LEDPulseTimerStart;
    //digitalWrite(PIN_TRIGGER_B, HIGH); //go high
    PORT_TRIGGER_LED |= (1 << PIN_TRIGGER_LED);
    PORT_TRIGGER_DROP &= ~(1 << PIN_TRIGGER_DROP);
    PORT_TRIGGER_SHUTTER |= (1 << PIN_TRIGGER_SHUTTER);

    break;

  case 2:

    TCNT3 = conf.LEDSecondTimerStart;

    PORT_TRIGGER_LED &= ~(1 << PIN_TRIGGER_LED);

    break;

  case 3:
    TCNT3 = conf.LEDPulseTimerStart;
    if (conf.secondPulseEnabled)
    {
      PORT_TRIGGER_LED |= (1 << PIN_TRIGGER_LED);
    }

    break;

  case 4:

    TCNT3 = conf.LEDDelayTimerStart;

    PORT_TRIGGER_LED &= ~(1 << PIN_TRIGGER_LED);
    PORT_TRIGGER_SHUTTER &= ~(1 << PIN_TRIGGER_SHUTTER);
    TIMSK3 = 0; //disable the interrupts so that this pulse is only seen once.
    nextFrame = millis() + conf.cameraMinFrameTime;
    frameLockout = true;

    break;

  case 5: //I think this does not ever run. but need to check.
    TIMSK3 = 0;
    TCNT3 = conf.LEDDelayTimerStart;
    PORT_TRIGGER_DROP &= ~(1 << PIN_TRIGGER_DROP);
    break;
  }

  if (triggerSeq >= maxTriggerSeq)
  {
    triggerSeq = 0;
  }
  else
  {
    triggerSeq++;
  }

  if ((triggerSeq == 1) && frameLockout) //special case - if we are locked out by the frame rate limit, then skip the LED pulse and camera trigger.
  {
    triggerSeq = 5;
  }
}




void loop()
{
  // Process serial data, and call functions if any commands if received.
  comm.run();

  // Feed the gcode handler serial data
  if (UARTPORT.available() > 0)
    comm.insert(UARTPORT.read());

  if (!stepper.getMotorState(POSITION_REACHED))
  {

    if (!targetReached)
    {
      comm.send("REACHED");
      targetReached = true;
    }
  }

  if (stepper.driver.getVelocity() == 0)
    stepper.moveSteps(0); // Enter positioning mode again

  handleProgressiveTrigger();
  handleLockout();
}

void handleProgressiveTrigger()
{
  if (conf.progressiveModeEnabled)
  {
    float theta = stepper.angleMoved();

    if (theta > conf.progAngleOffset + conf.progAnglePeriod)
    {
      trigger();
      conf.progAngleOffset += conf.progAnglePeriod;
    }

    if (theta < conf.progAngleOffset - conf.progAnglePeriod)
    {
      trigger();
      conf.progAngleOffset -= conf.progAnglePeriod;
    }
  }
}

/* 
 * --- GCode functions ---
 * Used by the GCode class to handle the different commands and send data
 */

void uart_send(char *data)
{
  UARTPORT.print(data);
}

void uart_default(char *cmd, char *data)
{
  comm.send("Unknown");
}

void uart_move(char *cmd, char *data)
{
  int32_t steps = 0;
  comm.value("A", &steps);

  stepper.setMaxVelocity(conf.velocity);
  stepper.moveSteps(steps);

  comm.send("OK");
}

void uart_moveto(char *cmd, char *data)
{
  float angle = 0.0;
  comm.value("A", &angle);

  stepper.setMaxVelocity(conf.velocity);
  stepper.moveToAngle(angle);
  target = angle;
  targetReached = false;

  comm.send("OK");
}

void uart_continuous(char *cmd, char *data)
{
  float velocity = 0.0;
  comm.value("A", &velocity);

  if (!strcmp(cmd, GCODE_CONTINUOUS))
    stepper.setRPM(velocity);
  else
  {
    stepper.setRPM(0);
  }

  comm.send("OK");
}

void uart_home(char *cmd, char *data)
{
  char buf[50] = {'\0'};
  char strAngle[12] = {'\0'};
  float railLengthAngle;

  float velocity = conf.homeVelocity;
  int32_t threshold = conf.homeThreshold;
  int32_t dir = conf.homeDirection;

  comm.value("V", &velocity);
  comm.value("T", &threshold);
  comm.value("D", &dir);

  conf.homeVelocity = velocity;
  conf.homeThreshold = (int8_t)threshold;
  conf.homeDirection = (bool)dir;

  stepper.moveToEnd(conf.homeDirection, conf.homeVelocity, conf.homeThreshold);                    //move to one end
  railLengthAngle = stepper.moveToEnd(!conf.homeDirection, conf.homeVelocity, conf.homeThreshold); //then move all the way back to the other end and measure how far it was
  stepper.encoder.setHome();                                                                       // Reset home position

  dtostrf(railLengthAngle, 6, 2, strAngle);

  strcat(buf, "DATA ");
  sprintf(buf + strlen(buf), "A%s", strAngle);
  comm.send(buf); // Tell GUI homing is done
}

void uart_stop(char *cmd, char *data)
{
  stepper.stop();
  comm.send("OK");
}

void uart_setbrake(char *cmd, char *data)
{
  if (!strcmp(cmd, GCODE_SET_BRAKE_FREE))
  {
    stepper.setBrakeMode(FREEWHEELBRAKE);
    conf.brake = FREEWHEELBRAKE;
  }
  else if (!strcmp(cmd, GCODE_SET_BRAKE_COOL))
  {
    stepper.setBrakeMode(COOLBRAKE);
    conf.brake = COOLBRAKE;
  }
  else if (!strcmp(cmd, GCODE_SET_BRAKE_HARD))
  {
    stepper.setBrakeMode(HARDBRAKE);
    conf.brake = HARDBRAKE;
  }
  comm.send("OK");
}

void uart_config(char *cmd, char *data)
{
  float value = 0.0;

  // If no value can be extracted dont change config
  if (comm.value("A", &value))
  {
    if (!strcmp(cmd, GCODE_SET_SPEED))
    {
      conf.velocity = value;
    }
    else if (!strcmp(cmd, GCODE_SET_ACCEL))
    {
      stepper.setMaxAcceleration(value);
      stepper.setMaxDeceleration(value);
      conf.acceleration = value;
    }
  }
}

void uart_setClosedLoop(char *cmd, char *data)
{
  if (!strcmp(cmd, GCODE_SET_CL_ENABLE))
  {
    stepper.moveSteps(0); // Set target position
    stepper.enableClosedLoop();
    conf.closedLoop = true;
  }
  else if (!strcmp(cmd, GCODE_SET_CL_DISABLE))
  {
    stepper.disableClosedLoop();
    conf.closedLoop = false;
  }
}

void uart_sendData(char *cmd, char *data)
{
  char buf[50] = {'\0'};
  char strAngle[10] = {'\0'};
  char strRPM[10] = {'\0'};
  char strDriverRPM[10] = {'\0'};

  int32_t steps = stepper.driver.getPosition();
  float angle = stepper.angleMoved();
  float RPM = stepper.encoder.getRPM();
  float driverRPM = stepper.getDriverRPM();

  dtostrf(angle, 4, 2, strAngle);
  dtostrf(RPM, 4, 2, strRPM);
  dtostrf(driverRPM, 4, 2, strDriverRPM);

  strcat(buf, "DATA ");
  sprintf(buf + strlen(buf), "A%s S%ld V%s D%s", strAngle, steps, strRPM, strDriverRPM);

  comm.send(buf);
}

void uart_sendConfig(char *cmd, char *data)
{
  char buf[50] = {'\0'};
  char strVel[10] = {'\0'};
  char strAccel[10] = {'\0'};
  char strHomeVel[10] = {'\0'};

  dtostrf(conf.velocity, 4, 2, strVel);
  dtostrf(conf.acceleration, 4, 2, strAccel);
  dtostrf(conf.homeVelocity, 4, 2, strHomeVel);

  strcat(buf, "CONF ");
  sprintf(buf + strlen(buf), "V%s A%s B%d C%d D%s E%d F%d", strVel, strAccel, conf.brake, conf.closedLoop, strHomeVel, conf.homeThreshold, conf.homeDirection);

  comm.send(buf);
}

void uart_sendTemp(char *cmd, char *data)
{
  char buf[50] = {'\0'};
  char strNozzle[10] = {'\0'};
  char strBed[10] = {'\0'};


  double c1 = thermocouple.readCelsius();
  double c2 = thermocouple2.readCelsius();

  dtostrf(c1, 4, 2, strNozzle);
  dtostrf(c2, 4, 2, strBed);

  strcat(buf, "TEMP ");
  sprintf(buf + strlen(buf), "N%s B%s", strNozzle, strBed);

  comm.send(buf);
}

void trigger()
{
  noInterrupts();
  TIMSK3 |= (1 << TOIE3);

  interrupts();
}

void uart_trigger(char *cmd, char *data)
{
  trigger();

  comm.send("OK");
}

void uart_configureTriggerTiming(char *cmd, char *data)
{

  int32_t LEDPulseLengthMicros = conf.LEDPulseLengthMicros;
  int32_t LEDDelayMicros = conf.LEDDelayMicros;
  int32_t LEDSecondMicros = conf.LEDSecondMicros;
  int32_t LEDPulseTimerStart = conf.LEDPulseTimerStart;
  int32_t LEDDelayTimerStart = conf.LEDDelayTimerStart;
  int32_t cameraMaxFPS = conf.cameraMaxFPS;
  int32_t LEDSecondTimerStart = conf.LEDSecondTimerStart;
  int32_t secondPulseEnabled = conf.secondPulseEnabled;

  comm.value("L", &LEDPulseLengthMicros);
  comm.value("D", &LEDDelayMicros);
  comm.value("S", &LEDSecondMicros);
  comm.value("T", &secondPulseEnabled);
  comm.value("F", &cameraMaxFPS);

  conf.LEDPulseLengthMicros = LEDPulseLengthMicros;
  conf.LEDDelayMicros = LEDDelayMicros;
  conf.secondPulseEnabled = secondPulseEnabled;

  conf.cameraMaxFPS = cameraMaxFPS;
  conf.cameraMinFrameTime = 1000 / cameraMaxFPS;

  conf.LEDPulseTimerStart = 65536 - (16 * (LEDPulseLengthMicros - TIMER_DELAY_COMPENSATION)); //derive value of OCR3A from the A Pulse Length. NB the -3 is just a fudge. minimum value of 12us currently!! max is about 4ms.
  conf.LEDDelayTimerStart = 65536 - (16 * (LEDDelayMicros - TIMER_DELAY_COMPENSATION));
  conf.LEDSecondTimerStart = 65536 - (16 * ((LEDSecondMicros - LEDPulseLengthMicros) - TIMER_DELAY_COMPENSATION));

  comm.send("OK");
}

void uart_configureTriggerProgressive(char *cmd, char *data)
{

  float progAngleOffset = conf.progAngleOffset;
  float progAnglePeriod = conf.progAnglePeriod;
  int32_t progressiveModeEnabled = conf.progressiveModeEnabled;

  comm.value("B", &progAngleOffset);
  comm.value("P", &progAnglePeriod);
  comm.value("T", &progressiveModeEnabled);

  progAngleOffset = stepper.angleMoved();

  conf.progAngleOffset = progAngleOffset;
  conf.progAnglePeriod = progAnglePeriod;
  conf.progressiveModeEnabled = progressiveModeEnabled;

  comm.send("Progressive Mode Configured OK");
}

void uart_configureTriggerContinuous(char *cmd, char *data)
{

  //store the old config values
  float continuousFrequency = conf.continuousFrequency;
  int32_t continuousOCR = conf.continuousOCR;
  int32_t continuousModeEnabled = conf.continuousModeEnabled;

  //if new ones are available, overwrite them
  comm.value("F", &continuousFrequency);
  comm.value("T", &continuousModeEnabled);

  //and apply them
  conf.continuousFrequency = continuousFrequency;
  conf.continuousModeEnabled = continuousModeEnabled;


  //calculate the value of OCR4A needed and apply it
  conf.continuousOCR = (F_CPU/256)/continuousFrequency;
  OCR4A = conf.continuousOCR;
}

/** Implemented on the WiFi shield */
void uart_record(char *cmd, char *data) {}

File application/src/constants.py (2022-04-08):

#Constants file for the bespoke IJP rig. lots of useful parameters here if you ever feel the need to tweak how it works...


#COM ports. eventually these won't need to be hardcoded...



JETDRIVE_PORT = 'COM1'
HEATER_PSU_PORT = 'COM7'

GET_BOUNDS_ON_STARTUP = False


dimMap = {0:'x',1:'y'}

LCDvals = {'axis':0,'angle':1,'steps':2,'V_measured':5,'V_target':4,'mm':3}

LETTER_TO_LCD = {'A':'angle','S':'steps','V':'V_measured','D':'V_target'}


#Heater LCD stuff

HeaterLCDvals = {'Channel':0,'VSET':1,'ISET':3,'VOUT':2,'IOUT':4}

HeaterChannelNames = {0:'nozzle',1:'bed'}

#motor settings

MICROSTEPPING = 256

WHOLE_STEPS_PER_REV = 200

STEPS_PER_REV = MICROSTEPPING*WHOLE_STEPS_PER_REV

#Physical parameters of the rail

RAIL_APPROX_LENGTH_STEPS = 700000

RAIL_APPROX_LENGTH_DEGREES = 5000

RAIL_DEGREES_TO_MM = 8/360

RAIL_MM_TO_DEGREES = 1/RAIL_DEGREES_TO_MM

RAIL_APPROX_LENGTH_MM = RAIL_APPROX_LENGTH_DEGREES*RAIL_DEGREES_TO_MM

TO_ANGLE_DICT = {'mm':RAIL_MM_TO_DEGREES,'angle':1,'steps':360/STEPS_PER_REV}

#temperature conversion

ARDUINO_MAX_RAW_ANALOG = 1023

ARDUINO_ANALOG_REFERENCE = 5.0

AD8495_OFFSET = -1.25

AD8495_DIVISOR = 0.005

#up, down, left and right

#WASD mappings

KEY_PRINTER_UP = 87
KEY_PRINTER_DOWN = 83
KEY_PRINTER_RIGHT = 68
KEY_PRINTER_LEFT = 65

KEY_TO_CHEVRON_DICT = {
    KEY_PRINTER_UP:'^',
    KEY_PRINTER_DOWN:'v',
    KEY_PRINTER_LEFT:'<',
    KEY_PRINTER_RIGHT:'>'
}

CHEVRON_TO_AXIS_DICT = {
            '^': 0,
            'v': 0,
            '>': 1,
            '<': 1,
            }

CHEVRON_TO_SIGN_DICT = {
            '^': -1,
            'v': 1,
            '>': -1,
            '<': 1,
            }


#Application GUI Settings

QT_REDIRECT_STDERR = False
QT_REDIRECT_STDOUT = False

QT_JOYPAD_WIDTH = 200
QT_JOYPAD_HEIGHT = 200

QT_XY_SETTER_WIDTH = 300

QT_JOYSTICK_MAXIMUM_STEPS = 1000000

QT_JOYSTICK_STEP_INCREMENT = 10000

QT_POLLER_ENABLED = 1

QT_POLLER_TIME_MS = 2000

QT_POLL_PSU = False

QT_STYLE_EXECUTE_READY = "background-color: green; color: white"

QT_STYLE_EXECUTE_RUNNING = "background-color: yellow; color: black"


WELCOME_MESSAGE = "Welcome to IEB Printing."

QT_MAIN_WINDOW_TITLE =  "bespoke-ijp"

#Power Supply Settings


POW_HEATER_NOZZLE_CHANNEL = 1
POW_HEATER_NOZZLE_INIT_VOLTAGE = 12
POW_HEATER_NOZZLE_MAX_VOLTAGE = 14
POW_HEATER_NOZZLE_MAX_CURRENT = 1.0

POW_HEATER_BED_CHANNEL = 3
POW_HEATER_BED_INIT_VOLTAGE = 5
POW_HEATER_BED_MAX_VOLTAGE = 10
POW_HEATER_BED_MAX_CURRENT = 0.9

POW_SERIAL_TIMEOUT = 0.01

#Control Loop stuff

PID_PROPORTIONAL_ON_MEASUREMENT = False

QT_SHOW_PID_TERMS = True

# Proportional Integral and Derivative terms

PID_P = 0.5
PID_I = 0.01
PID_D =  4.0



""" paramaters for metal slide holder
PID_P = 1.0
PID_I = 0.02
PID_D =  4.0
"""

""" parameters for flat heat plate on old nozzle holder (angled)
PID_P = 1
PID_I = 0.05
PID_D =  0.05

"""

#uStepper Axis responsible for trigger control

TRIGGER_AXIS = 0

TRIGGER_MAX_TIME = 10000

TRIGGER_MIN_TIME = 10

#uStepper Axis responsible for temperature readouts
TEMP_AXIS = 0

TEMP_SETPOINT = 20 #default temperature setpoint

GRAPH_TEMP_WIDTH = 50 #number of successive points to plot on graph


#AFG2021 settings

AFG2021_VISA_PORT = 'USB::0x0699::0x0349::C013148::INSTR'

#AFG-2105 settings



#grid settigns

GRID_TIME_DELAY_MS = 1000

GRID_POLL_MS = 1000

BURST_TIME_DELAY_MS = 200

GRID_BACKLASH_COMPENSATION_ENABLED = True
GRID_BACKLASH_COMPENSATION_STEPS = 1000

GRID_MAX_DROPS = 50

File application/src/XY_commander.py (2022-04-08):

from PySide2.QtWidgets import (
    QApplication,
    QWidget,
    QPushButton,
    QVBoxLayout,
    QLabel,
    QPlainTextEdit,
    QTextEdit,
    QCheckBox,
    QHBoxLayout,
)
from PySide2.QtWidgets import (
    QGridLayout,
    QLineEdit,
    QMainWindow,
    QSpinBox,
    QLCDNumber,
    QGroupBox,
    QDoubleSpinBox,
)
from PySide2.QtCore import Slot, Qt, QTimer, QDateTime, Signal, QObject, Signal
from PySide2.QtGui import QTextCursor
import sys
from functools import partial
import serial
import serial.tools.list_ports
import re
import photofluor
from constants import *


import time


import conversions as conv

import numpy as np

import random
import datetime as dt
import matplotlib

matplotlib.use("Qt5Agg")

from matplotlib.backends.backend_qt5agg import FigureCanvasQTAgg
from matplotlib.figure import Figure


from SequenceHandler import *
import psu_serial
from XYSerialInterface import *
from HeaterPIDController import *



class EmittingStream(QObject):

    textWritten = Signal(str)

    def write(self, text):
        self.textWritten.emit(str(text))



class MplCanvas(FigureCanvasQTAgg):
    """summary

    :param FigureCanvasQTAgg: [description]
    :type FigureCanvasQTAgg: [type]
    """

    def __init__(self, parent=None, width=5, height=4, dpi=100):
        fig = Figure(figsize=(width, height), dpi=dpi)
        self.axes = fig.add_subplot(1, 2, 1)
        self.axes2 = fig.add_subplot(1, 2, 2)
        super(MplCanvas, self).__init__(fig)


class GraphWindow(QWidget):
    """
    This "window" is a QWidget. If it has no parent, it
    will appear as a free-floating window as we want.
    """

    def __init__(self):
        super().__init__()
        layout = QVBoxLayout()
        self.label = QLabel("Graphs!")
        layout.addWidget(self.label)
        self.setLayout(layout)
        n_data = 50
        self.xdata = list(range(n_data))
        self.ydata = [random.randint(0, 80) for i in range(n_data)]

        n_data = 50
        self.xdata2 = list(range(n_data))
        self.ydata2 = [random.randint(0, 80) for i in range(n_data)]

        self.sc = MplCanvas(self, width=5, height=4, dpi=100)

        layout.addWidget(self.sc)

        self._plot_ref = None
        self._plot_ref_2 = None

        self.show()

    def update_plot(self, y_new):
        self.ydata = self.ydata[1:]
        self.ydata.append(y_new)
        if self._plot_ref is None:
            # First time we have no plot reference, so do a normal plot.
            # .plot returns a list of line <reference>s, as we're
            # only getting one we can take the first element.
            plot_refs = self.sc.axes.plot(self.xdata, self.ydata, "r", label="bed")
            self._plot_ref = plot_refs[0]
        else:
            # We have a reference, we can use it to update the data for that line.
            self._plot_ref.set_ydata(self.ydata)

        # Trigger the canvas to update and redraw.
        self.sc.draw()

    def update_other_plot(self, y_new):
        self.ydata2 = self.ydata2[1:]
        self.ydata2.append(y_new)
        if self._plot_ref_2 is None:
            # First time we have no plot reference, so do a normal plot.
            # .plot returns a list of line <reference>s, as we're
            # only getting one we can take the first element.
            plot_refs = self.sc.axes.plot(self.xdata2, self.ydata2, "r", label="bed2")
            self._plot_ref_2 = plot_refs[0]
        else:
            # We have a reference, we can use it to update the data for that line.
            self._plot_ref_2.set_ydata(self.ydata2)

        # Trigger the canvas to update and redraw.
        self.sc.draw()


class TriggerWindow(QWidget):
    def __init__(self, label="untitled"):
        super().__init__()
        layout = QHBoxLayout()

        self.setWindowTitle("Trig. Config")

        self.label = label

        layout.addWidget(self.createTimingBox())
        layout.addWidget(self.createProgressiveBox())
        layout.addWidget(self.createContinuousBox())

        self.setLayout(layout)
        self.setWindowFlags(Qt.Tool)
        self.createShowButton()
        # self.core = TriggerWindow(label = label)

    def createProgressiveBox(self):
        progressiveLayout = QVBoxLayout()
        progressiveBox = QGroupBox("Progressive")

        self.progressiveModeCheckBox = QCheckBox("Enable")
        progressiveLayout.addWidget(self.progressiveModeCheckBox)
        progressiveLayout.addWidget(QLabel("Distance/mm"))
        self.progressiveMMPeriodSpin = QDoubleSpinBox(minimum=0.01, maximum=100, suffix = " mm", singleStep = 0.01)
        progressiveLayout.addWidget(self.progressiveMMPeriodSpin)

        progressiveBox.setLayout(progressiveLayout)
        return progressiveBox

    def createContinuousBox(self):
        layout = QVBoxLayout()
        box = QGroupBox("Continuous")

        self.continuousModeCheckBox = QCheckBox("Enable")
        layout.addWidget(self.continuousModeCheckBox)
        layout.addWidget(QLabel("Frequency"))
        self.continuousFrequencySpin = QSpinBox(minimum=1, maximum=1000, suffix = " Hz", singleStep = 1)
        layout.addWidget(self.continuousFrequencySpin)

        box.setLayout(layout)


        return box

    def createTimingBox(self):
        timingLayout = QVBoxLayout()
        timingBox = QGroupBox("Timing")

        timingLayout.addWidget(QLabel("Camera Max FPS"))
        self.CameraFPSSpin = QSpinBox(minimum = 1, maximum = 120)
        self.CameraFPSSpin.setValue(20)
        timingLayout.addWidget(self.CameraFPSSpin)

        timingLayout.addWidget(QLabel("LED Delay/us"))

        self.LEDDelaySpin = QSpinBox(minimum=TRIGGER_MIN_TIME, maximum=TRIGGER_MAX_TIME)
        timingLayout.addWidget(self.LEDDelaySpin)

        timingLayout.addWidget(QLabel("LED Exposure/us"))

        self.LEDExposureSpin = QSpinBox(
            minimum=TRIGGER_MIN_TIME, maximum=TRIGGER_MAX_TIME
        )
        timingLayout.addWidget(self.LEDExposureSpin)

        timingLayout.addWidget(QLabel("Second Strobe Delay/us"))

        self.LEDSecondSpin = QSpinBox(
            minimum=TRIGGER_MIN_TIME + 10, maximum=TRIGGER_MAX_TIME
        )
        timingLayout.addWidget(self.LEDSecondSpin)
        self.setButton = QPushButton("SET")
        # layout.addWidget(self.setButton)

        self.secondPulseEnable = QCheckBox("Double Pulse")
        timingLayout.addWidget(self.secondPulseEnable)

        timingBox.setLayout(timingLayout)

        return timingBox

    def toggle(self):
        if self.isVisible():
            self.hide()
        else:
            self.show()

    def createShowButton(self):
        showLabel = "Trig. Config"
        self.showButton = QPushButton(showLabel)
        self.showButton.clicked.connect(partial(self.toggle))
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

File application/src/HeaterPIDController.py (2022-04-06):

from matplotlib.backends.backend_qt5agg import FigureCanvasQTAgg
from matplotlib.figure import Figure
from simple_pid import PID
from PySide2.QtWidgets import QApplication, QWidget, QPushButton, QVBoxLayout, QLabel, QPlainTextEdit, QHBoxLayout
from PySide2.QtWidgets import QGridLayout, QLineEdit, QMainWindow, QSpinBox, QLCDNumber, QGroupBox, QDoubleSpinBox
from PySide2.QtCore import Slot, Qt, QTimer,QDateTime, Signal
from constants import *

from functools import partial
class HeaterPIDController():
    def __init__(self,PSUchannel,name,PSUcontroller,sample_time,max_current,max_voltage):
        self.pid = PID(PID_P, PID_I, PID_D, setpoint = TEMP_SETPOINT, output_limits=(0,max_voltage),proportional_on_measurement=PID_PROPORTIONAL_ON_MEASUREMENT, sample_time=sample_time)
        self.output = PSUcontroller
        self.channel = PSUchannel
        self.output.power.set_current(max_current, self.channel)

        self.output.power.turn_off()
        
        self.temperature = 0

        self.last_control = -1
        

        self._ui = PID_Layout(label = name)
        


        self._connectSignals()
        self._ui.graph.update_plot(0,0,0,0,0,0)
        #self.update(0)

    def getNewSetpointFromUI(self):
        """Retrieve the setpoint from the UI and pass it to the control loop. Then turn on the PSU.
        """
        new_t = int(self._ui.setter.setpointSpin.text())
        
        self.set_setpoint(new_t)

        self.output.power.turn_on()
        return

    def _connectSignals(self):
        """Setup function - connects signals and slots for UI components.
        """
        self._ui.setter.setpointButton.clicked.connect(partial(self.getNewSetpointFromUI))
        return

    def update(self,t):
        """Update the PID controller with the most recent temperature reading

        :param t: Latest temperature reading
        :type t: float
        """        
        self.temperature = t
        if self.output.power.is_on: #we should only run the pid loop if the heater is actually on
            control = self.pid(t)
            p, i, d = self.pid.components
        else: # if the heater is off, just set everything to zero
            control = 0
            p = 0
            i = 0
            d = 0
        if control is not self.last_control: #to minimise use of the serial port, only tell the heater the new voltage if it is different to the old one
            self.set_voltage(control)
            self.last_control = control
        #print(self.pid.components)
        #print('T: ' + str(t) +' V: ' + str(control))
        
        

        self._ui.graph.update_plot(t, control,self.get_setpoint(), p, i, d)
        self._ui.setter.update(t,self.get_setpoint())

    def get_setpoint(self):
        """Return the temperature setpoint

        :return: temparature setpoint in deg C
        :rtype: float
        """        
        return self.pid.setpoint

    def get_last_temperature(self):
        """Returns the most recent temperature measurement

        :return: latest temperature reading in deg C
        :rtype: float
        """        
        t = self.graph.tdata[-1]
        return t

    def set_setpoint(self, sp):
        """Set the temperature setpoint

        :param sp: setpoint in deg C
        :type sp: float
        """        
        self.pid.setpoint = sp


    def show_graphs(self):
        return
        self.graph.show()



    def set_voltage(self,v):
        """Set the output voltage. Possibly deprecated.

        :param v: voltage
        :type v: float
        """        
        ch = self.channel
        #v = int(v)
        v = round(v,1)
        #v = "%0.1f" % v
        msg = "VSET" + str(ch) + ":" + str(v) + "\n"
        #print(msg)
        
        self.output.power.get_custom(msg,'NOREPLY')
        #print(self.output.power.get_custom(msg,'REPLY'))

class PID_Layout(QWidget):
    def __init__(self, label = "untitled"):
        super().__init__()
        layout = QHBoxLayout()
        #self.windowTitle = label
        self.setWindowTitle('Heater Control: ' + label)
        self.label = label
        self.setLayout(layout)

        self.graph = PIDGraphWindow(label = label)
        self.setter = PID_Setter(label = 'Controls')
        layout.addWidget(self.graph)
        layout.addWidget(self.setter)
        self.createShowButton()
        self.setWindowFlags(Qt.Tool)
        self.setMaximumHeight(0)








        #self.show()


    def toggle(self):
        if self.isVisible():
            self.hide()
        else:
            self.show()


    def createShowButton(self):
        showLabel = 'Heater Control: ' + self.label
        self.showButton = QPushButton(showLabel)
        self.showButton.clicked.connect(partial(self.toggle))
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

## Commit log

2021-02-11 add util to list attached serial devices
2021-02-11 add PSU tracking functions - minor issue with error messages though.
    [XY_commander.py, constants.py, psu_serial.py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]
2021-02-12 add temperature readout, fix issue with polling PSU
    [XY_commander.py, XY_driver_G.ino, constants.h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]
2021-02-12 add temperature graphs
2021-02-12 remove temperature printing
2021-02-13 more documentation added inc poweron procedure
2021-02-13 even more docs, including some build instructions and poweron procedure
2021-02-16 warp scripts in init main conditional
    [plotter_example.py, port_finder.py, testpsu.py]
2021-02-19 temp fix for PSU issue, rearrange UI
    [XY_commander.py, constants.py, psu_serial.py]
2021-02-19 tuning pid
2021-02-23 generalise PID controller to separate windows
2021-02-23 add backlash issue
2021-03-01 add thorlabs half inch mirror
    [ME05S-G01-Solidworks.sldprt]
2021-03-08 made a holder for microscope slides
    [crude-slide-holder.SLDPRT]
2021-03-08 made a half inch thorlabs mirror holder
    [mirror-holder.SLDPRT]
2021-03-08 fillet and label crude slide holder
    [crude-slide-holder.SLDPRT]
2021-03-08 create perpendicular stage holder
    [stage-perp-holder.SLDPRT]
2021-03-08 add older CAD designs, rearrange hardware folder
    [C-Beam End Mount.SLDDRW, C-Beam End Mount.SLDPRT, C-Beam End Mount.step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]
2021-03-11 add more 3dp optical parts
    [42mm-polariser-holder-a.SLDPRT, navitar-support.SLDPRT, photofluor-holder.SLDPRT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]
2021-03-15 add phlatlight parts
    [Phlatlight-template.SLDPRT, phlatlight-led-holder.SLDPRT]
2021-03-17 add microfab nozzle schematic (inches)
2021-03-17 add placeholder element for photofluor head
    [photofluor-head.SLDPRT]
2021-03-23 add optical parts
    [calibrator.DXF, calibrator.SLDPRT, pf and nozzle holder.SLDPRT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]
2021-03-24 add TIMER3 based single-shot trigger
2021-03-24 add timer3 based dual trigger
2021-03-31 add PCINT2 interrupt and move trig out to 7, 8
2021-03-31 clarify workings of PCINT interrupts
2021-03-31 first draft of progressive print mode
2021-04-15 add toggle switch for second LED pulse
2021-04-15 embedded code for second LED pulse
2021-04-15 increase radius of angled nozzle holder
    [pf and nozzle holder.SLDPRT]
2021-04-15 replace external thread w/ internal thread #10
    [42mm-polariser-holder-a.SLDPRT, navitar-support.SLDPRT]
2021-04-15 alter phlatlight base to mount onto an optical table
    [phlatlight-pcb-base.SLDPRT]
2021-04-15 add sketch of photofluor holder
    [photofluor-holder.SLDDRW]
2021-04-15 fix prog mode overshoot on enable
    [XY_commander.py, XY_driver_G.ino, constants.h]
2021-04-25 improve failover for when no stage attached
    [XYSerialInterface.py, XY_commander.py]
2021-05-13 add error message for failed PSU data grab
    [XY_commander.py]
2021-06-08 change drop, led and camera trigger outputs to D3, D4 and A0 respectively
2021-06-08 intergrate digital temperature control with ustepper code
2021-06-11 tweak PID and enable PoM mode
2021-06-11 add comments on thermocouple grounding
2021-06-16 add 3d models of motor offset and new phlatlight holder
    [motor-offset.SLDPRT, phlatlight-pcb-holder.SLDPRT, phlatlight-standoff.SLDPRT]
2021-06-16 add notes on camera software
2021-06-30 alter phlatlight holder to better fit table
    [phlatlight-pcb-holder.SLDPRT]
2021-07-02 thin out holes in motor offset
    [motor-offset.SLDPRT]
2021-07-02 create new complex slide holder system
    [c-beam-to-6mm-optical-adapter-plate.SLDPRT, complex-slide-holder-A.SLDPRT, complex-slide-holder-B.SLDPRT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]
2021-07-04 add full assembly of xy stage and other CAD parts
    [120 Angle Tee Nut.SLDPRT, 135 Angle Tee Nut.SLDPRT, 2 Way Tee Nut.SLDPRT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]
2021-07-05 minor tweaks to pf and nozzle holder
    [pf and nozzle holder.SLDPRT]
2021-07-05 further corrections to pf-nozzle holder
    [pf and nozzle holder.SLDPRT]
2021-07-05 minor tweak to hole separation in pf and nozzle holder
    [pf and nozzle holder.SLDPRT]
2021-07-05 change heater mount holes to threads
    [pf and nozzle holder.SLDPRT]
2021-07-05 add new small printhead
    [new-small-printhead.SLDPRT]
2021-07-05 move old EP designs
    [microfab heating sheath Large.SLDDRW, microfab heating sheath Large.SLDPRT, microfab heating sheath.SLDDRW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]
2021-07-05 add engineering drawing of new small printhead
    [new-small-printhead.SLDDRW]
2021-07-07 tweaks to slide holder assembly based on feedback from first print
    [c-beam-to-6mm-optical-adapter-plate.SLDPRT, complex-slide-holder-A.SLDPRT, complex-slide-holder-B.SLDPRT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]
2021-07-07 further tweaks to complex slide holder
    [complex-slide-holder-B.SLDPRT, complex-slide-holder-assy.SLDASM]
2021-07-21 add laser cut offset parts
    [printhead-offset-finger.SLDPRT, printhead-offset-finger_1.DXF, printhead-offset-finger_2.DXF]
2021-07-21 add thicker optical adapter
    [printhead-offset-finger_3.DXF]
2021-07-23 rework most CAD files, add vertical stage
    [LED-holder-assy-lefthand.SLDASM, LED-holder-assy-righthand.SLDASM, Phlatlight-template.SLDPRT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]
2021-08-17 add substantial hardware revisions
    [L490_M-Solidworks.sldprt, LED-holder-assy-righthand.SLDASM, complex-slide-holder-assy.SLDASM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]
2021-08-26 more hardware work
    [LED-holder-assy-righthand.SLDASM, clip-and-metal-slide-holder.SLDASM, complex-slide-holder-assy.SLDASM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]
2021-09-08 add new heated slide holder
    [heated-slide-holder.SLDDRW, metal-slide-holder.SLDDRW, metal-slide-holder.SLDPRT]
2021-10-05 add 3d printed ITO etching templaets
    [etching-template.SLDPRT, ito-clipper.SLDPRT]
2021-10-05 add thorlabs icroscope holder
    [OMR_M-Solidworks.sldprt]
2021-10-06 retune and improve PID for new heat element
2021-10-06 remove printing of deltas on some motion funcs
2021-10-06 add grid-printing macro with backlash comp
    [XY_commander.py]
2021-10-07 QOL improvements to heater control
2021-10-08 switch power supply off on exit
2021-11-04 QOL improvements to heater control and swap to CH3
    [HeaterPIDController.py, XY_commander.py, constants.py]
2021-12-13 better exception handling for stepper connection
2024-11-05 hardware updates for thesis
    [23-33-U-series-cmos.stp, 50.8mm-polariser.SLDPRT, 8mm Acme Anti Backlash Nut Block.SLDPRT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]
